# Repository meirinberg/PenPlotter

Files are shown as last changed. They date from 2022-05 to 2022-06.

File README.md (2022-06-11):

# Pen Plotter
<p align="center">
Mechanical Engineering 405 - Mechatronics <br> 
Term Project <br> 
Created by Mike Eirinberg, Ben Bradley, and Ryan Dean
</p>
<br>
<p align="center">
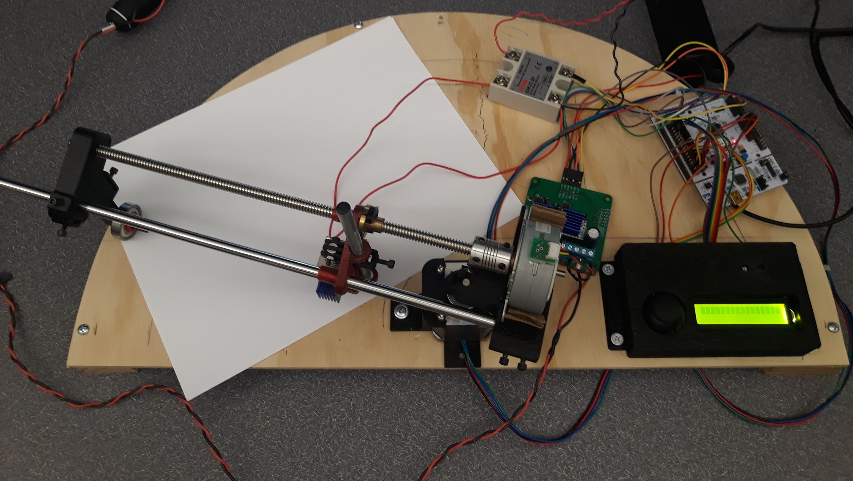
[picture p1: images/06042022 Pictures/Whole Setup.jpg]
  
</p>

## Demonstration
A demonstration of our pen plotter can be found using the following links. The first link demonstrates all features of our pen plotter and its attempt to draw a triangle. As discussed in the video, the motors provided by our mechatronics course were old and occasionally lock up. As a result, sometimes the drawing can't be finished. However, the second video shows a successful demonstration of the plotter drawing a triangle.

Pen Plotter Demonstration and Triangle-Drawing Attempt: <br>
https://youtu.be/bnkg2Q-DLaM

Succesful Triangle-Drawing Attempt:<br>
https://youtu.be/nqa20NQLPtA

## Project Background

In mechatronics, we were tasked with creating a 2.5 degree-of-freedom non-Cartesian pen plotter with the following rules. The pen plotter: 

1. Must be able to draw something
2. Must move in two different degrees of freedom (non-Cartesian)
3. Must use stepper motors for 2 axes
4. Must run off of 24V benchtop power supplies drawing no more than 6A
5. Must be safe (generally no lasers, fire, or hazarderous systems)

## Proposal
This project uses basic polar coordinates to accomplish drawing. The following image displays our initial sketch of our project’s hardware. Even though the structure of each component has been substantially refined, the core function can still be demonstrated in the sketch. It consists of a pivot point in the ‘Angular Subsystem’ sketch serving as the origin about which all major drawing components rotate. The ‘Radial Subsystem’ is an arm that extends overhead across the drawing area and provides structure for moving the pen. At the end, there is a T-shaped support structure with a wheel on the bottom. The wheel minimizes the friction required to start rotating the radial subsystem about the angular subsystem. We decided to use a support structure, because without it there would be a moment experienced by the angular motor rotor when the pen holder would be greatly extended in the radial direction. This could ultimately make it more difficult to move the motors and add drooping to the system. The next subsystem is the pen holder. This holds and activates the pen as it, using a lead screw, moves along the radial subsystem. The pen is pressed down by a solenoid upon activation.

<p align="center">
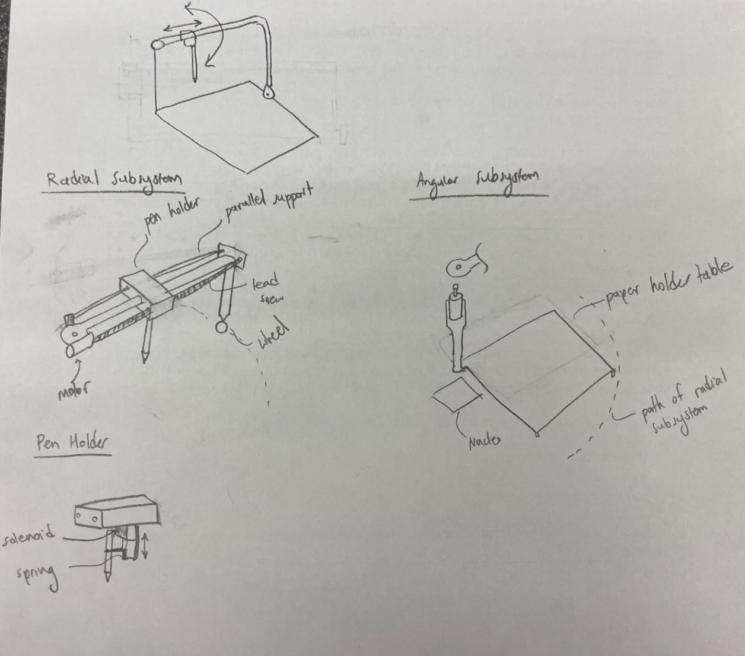
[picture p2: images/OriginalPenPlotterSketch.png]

</p>
<p align="center">
Figure 1. Initial sketch of pen plotter system
</p>

## First Iteration Challenges
We decided to use a 3D printer to create the parts that interact with the motors. Our first prints revealed critical flaws in our design. The first iteration prints can be seen below.
<p align="center">
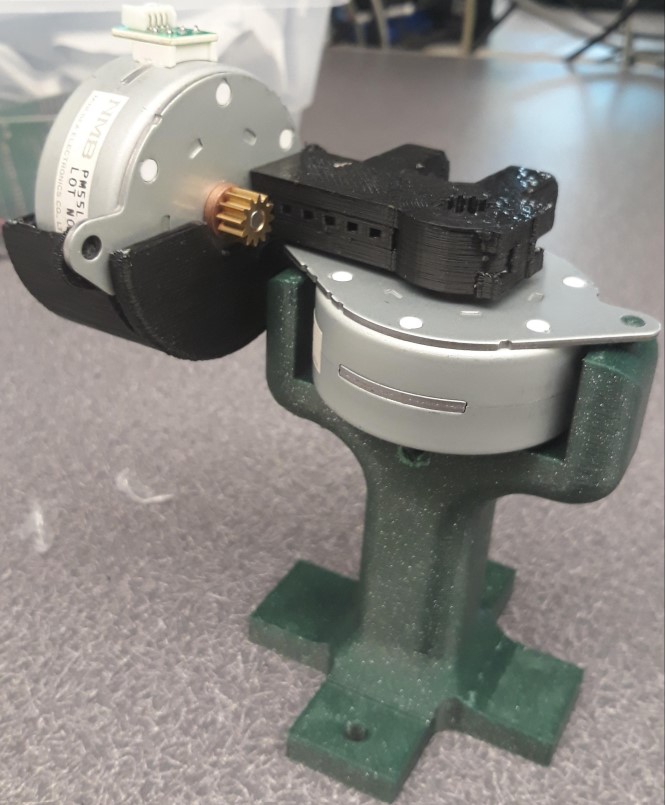
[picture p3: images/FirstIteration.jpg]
  
</p>
<p align="center">
Figure 2. First iteration 3D prints with radial and angular motor
</p>
We discovered that the pen plotter's resolution would face significant issues. Upon considering the dimensions of our drawing space, we realized that the angular motor would need to have very high accuracy. This is because resolution decreases as the pen moves farther out radially with each angular change. The provided motors only have 48 steps per revolution (7.5 degrees/step). This was far too low for our design, so we found a NEMA 17 stepper motor with 200 steps (1.8 degrees/step). This was a critical design challenge, because it caused us to change most radial motor design. The radial motor had to be properly secured. However, we did not change the radial motor to a NEMA 17 because our lead screw had a pitch of 2mm. Because of this, even with 48 steps, this small pitch allowed for higher resolution radial advancement. The pitch forced the radial motor to spin a lot to move linearly along the lead screw.

## Construction and Final Design
### Mechanical Design
A CAD model of our final design can be seen below. All part files and assemblies can be found in the 'parts' folder. See the images below for more details. Our construction consisted of 3D printing virtually all parts or reusing parts from past projects. A lead screw set, solenoid, and joysick were the only purchased parts.
<p align="center">
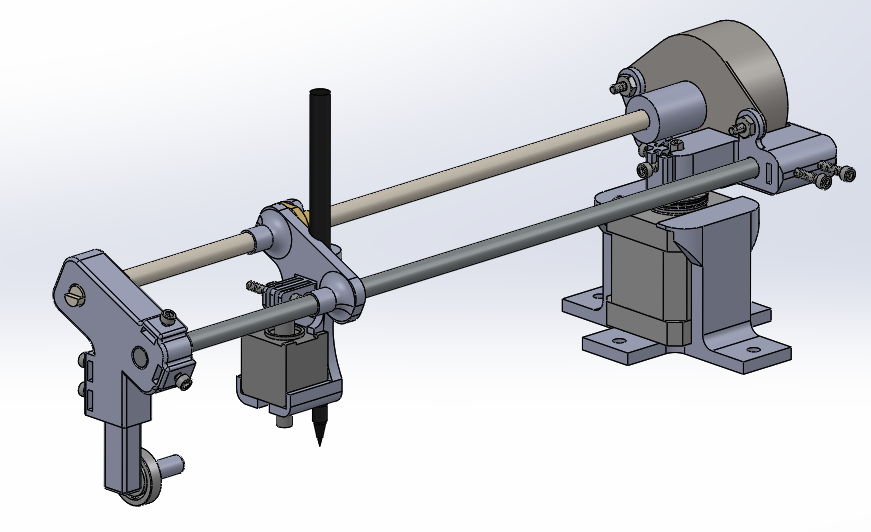
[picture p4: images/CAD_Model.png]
  
</p>
<p align="center">
Figure 3. CAD model of final design
</p>

Our final design closely follows the core concept of our initial sketch and accounts for the different geometry of using a NEMA 17 motor in our angular subsystem. This angular system is mounted in the center of a semicircle drawing canvas, and angularly rotates the radial system at its base to sweep angularly across the drawing area. We do not make use of the entire semicircle, since part of it will be used as space for the electronics. 
<br>

Our final design still consists of a solenoid to actuate the pen as well as a set screw for finding optimal pen height. It is critical for the design of this system to minimize friction, which may prevent the pen from actuating. This is because a solenoid has a starting force when it first begins to move and a holding force when it is fully extended. The starting force is the smallest since the solenoid is just beginning to actuate and can't experience the full effect of the induced magnetic field. Providing adequate clearance and guide structures allow for the pen to be rigidly actuated under the starting force. Our angular (theta) motor’s mount has a wide base to provide as much support as possible. Thrust bearings are used between the theta and radial motor assembly to further minimize angular friction during drawing. 
<br>

Because of the shaft-support structure, we don’t have to worry about the large moment created on the theta motor when the pen is far out along the lead screw, but this also increases the moment of inertia, making it harder for the theta motor to start rotating. A big design consideration was to make the system as adjustable as possible. There are many set screws around the assembly to make it easier to adjust lengths, heights, and replace components. The rest of the system is labeled below. 

<p align="center">
  
   
</p>
<p align="center">
Figure 4. Labeled components of mechanical design
</p>

### Electrical Design
Looking at the electrical components of our project, we were provided a Nucleo L476RG and a custom-made power board with a TMC4210 and TMC2208 motor driver per stepper motor. The TMC4210 interprets position, velocity, and acceleration commands, then sends step and direction signals to the TMC2208. The TMC2208 then takes this information and sends the appropriate current to the stepper motors. For each TMC2208, the voltage reference (Vref) needs to be set to create an internal current limit for the electrical components and stepper motors. We adjusted this by twisting a screw on the TMC2208 until we measured 0.7V. Datasheets for these components can be found in the folder above.

A 24V power supply is hooked up to the power board to supply power to the motors. For the solenoid, we used a solid-state relay and a separate power source, because of the solenoid's different power requirements. As seen in the image below, a joystick and LCD were also used as a user interface. As will be discussed later, these work together to select drawing files and control the free-draw feature.
<p align="center" float="left">
  
</p>
<p align="center">
Figure 5. Labeled components of electrical design
</p>

## Wiring Diagram
We used pinhole soldier boards for our hardware with trimmed leads. This ensured that we would not have a faulty connection, due to poor breadboard conductivity, while minimizing our resistances through smaller wires. This resulted in a wiring that never faultered. This wiring is modeled below. We communicate with our hardware using [Thonny](https://thonny.org/) connected to a laptop through a usb to micro usb connection. This powered our microcontroller, the STM32, which was the brains of our project. The STM32 had an attached "Shoe of Brian" to allow us to use micropython for this project. We utilized micropython to poll our joystick and send data to our LCD. The STM32 also controlled the pen through a solenoid that was attached to a relay. The power board contained two TMC4210s and two TMC2208s.  

<p align="center">
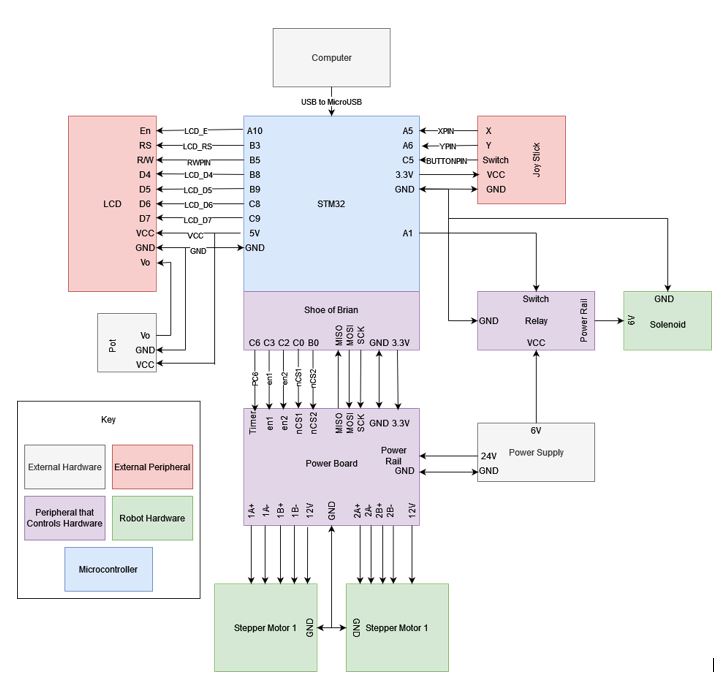
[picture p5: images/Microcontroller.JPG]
  
</p>
<p align="center">
Figure 6. Detailed wiring diagram
</p>

## Software Design and Implementation
Our code was structured as a finite state machine (FSM) using cooperative multitasking. We use five states, with the main four controlling the user interface, image processing, and sending motor commands in various modes. The FSM can be seen below with each state showing its task period and priority. The scheduler works by running based on frequency and priority, running the highest priority task at each call. Each state’s implementation will be discussed in further detail below.
<p align="center">
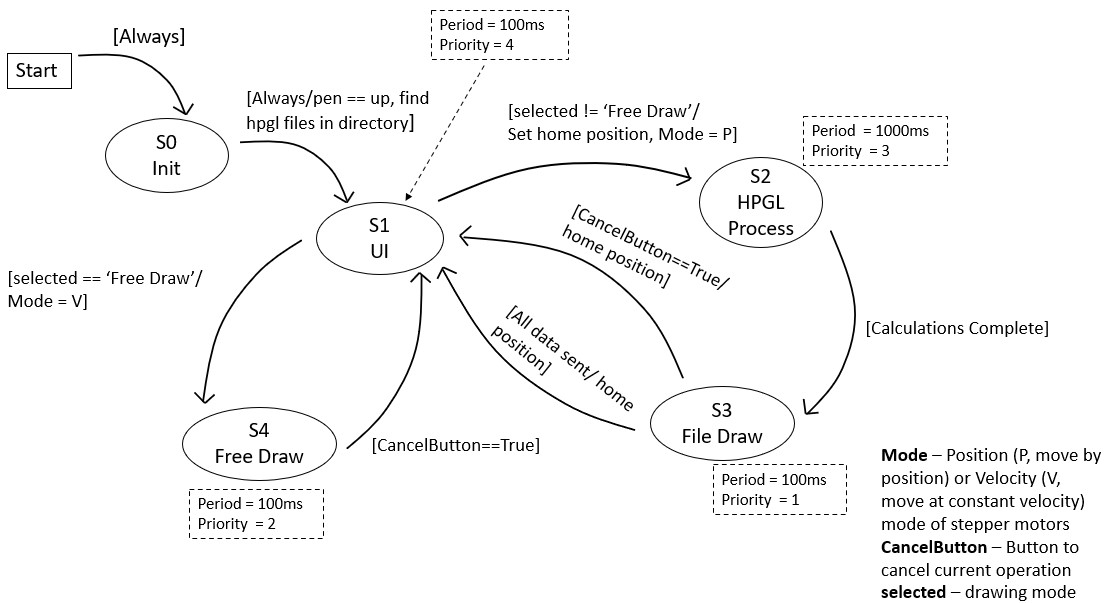
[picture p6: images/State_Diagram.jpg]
  
</p>
<p align="center">
Figure 7. State transition diagram
</p>

### S1 – User Interface
We designed our program to include an LCD-based user interface. This took some thoughtful programming. The user can scroll through the list of options by using the joystick axes and clicking the joystick to make a selection. Using the custom LCD class that we programmed, we sent one menu item to each line of the screen. We added a ">" character to prefix one menu option as a way for the user to highlight the item they wished to select. The program uses indexing to know which choice the user has highlighted and selected. To implement the scroll look, the program chooses which items to present in the list, one for each line. If the user has reached the top or bottom of the list, the scrolling ability stops.

The first menu item is always "Free Draw," which will put the program into that mode when selected. The next menu items are loaded from a basic file explorer function we programmed. The file explorer opens the current directory and finds the files with a .hpgl extension. It then lists those HP-GL files as the next menu items. Clicking an HP-GL file will cause the program to run file-draw mode using that filename.

The blue button on the STM32 microcontroller acts as our in-print cancellation button. By clicking this button during an active print, the pen plotter will return to its starting position and display the main menu user interface. When pressed during the free-draw mode, it will only cancel the mode, but not return to any position.

### S2 – Image Processing
This state receives the file name selected in the user interface to read the appropriate HP-GL data from a file stored on the board. The image-processing state can take a long time depending on the complexity of the image. Therefore, it was given the largest period in our task manager. This state calculates all required motor position data in one go and stores it as a global variable to be accessed from the file-draw state. 

All image-processing code was derived using the [Newton Raphson](#newton-raphson) method based on [Kinematic](#Kinematics) analysis. This analysis is discussed later. A key part of image processing was using linear interpolation. Due to the requirements of the system, the motors will spin at different rates. This means that over long distances, the motors can reach their target location at different times. This warps the image, so interpolation between the data points can be used to offset the effect. We first looked at the distance between points and saw if they passed certain thresholds. Various thresholds require different degrees of interpolation, with larger distances requiring more data points. This is accomplished using the linspace() function inherent to Python. Once interpolated and with the values added back to the original set, the data could then be sent to the file-draw state.

### S3 – File Draw
Once image processing is complete, this state will index through all the motor angle data and send the commands to the power board's drivers to run the stepper motors. Once the command is sent, our code reads the current position of the motors and will only continue indexing once they have reached their desired positions. The stepper motors are initialized in ramp mode for this state, since we need to send position data.

### S4 – Free Draw
The free-draw mode allows for manual drawing using a joystick. The user can control the pen-plotter directly, drawing anything they desire. X-direction joystick motion controls the theta motor while the Y-direction joystick motion controls the radial motor. Clicking the joystick will actuate the solenoid to force the pen up or down onto the paper. The stepper motors are initialized in velocity mode for this state and a virtual threshold for the joystick was hardcoded. This means that when the joystick passes a certain point, the motors will move at constant velocity. The threshold also helps with noise, as a resting joystick without a threshold could sporadically send signals.

## Kinematics

We used the following image to determine the calculations for our system. The image is viewed from the top looking down onto the drawing board. The ${\theta_1}$ represents the angular change of the arm while ${\theta_2}$ represents the angular change of the radial motor required to move the pen in the radial direction. This analysis should align with any polar-based system. 

<p align="center">
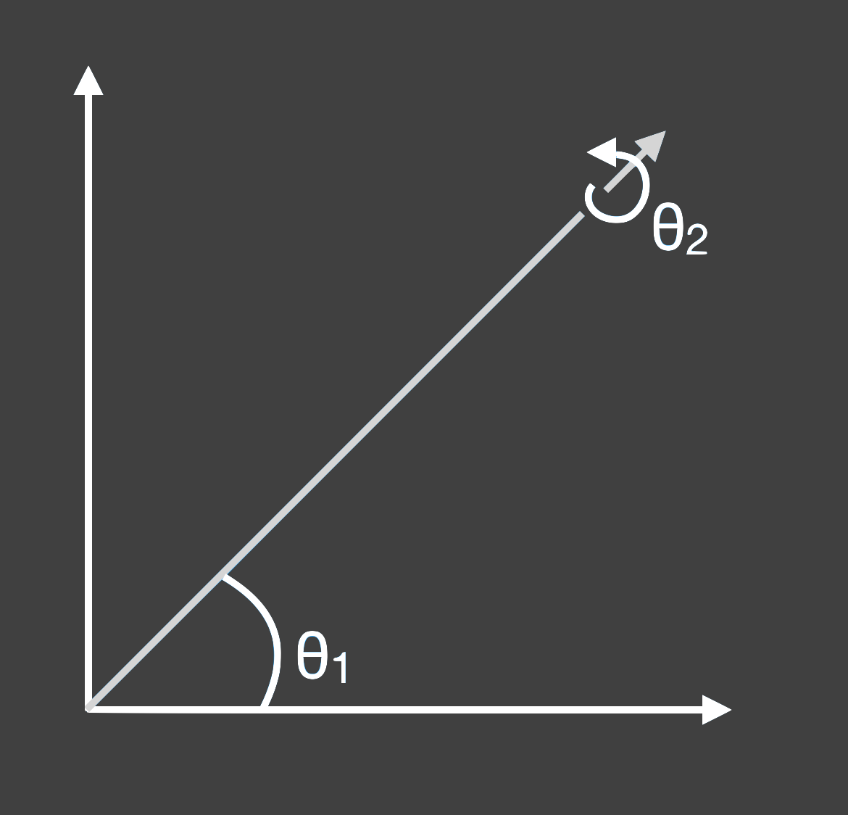
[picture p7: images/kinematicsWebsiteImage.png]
  
</p>
<p align="center">
Figure 8. Diagram of primary variables used in kinematic analysis
</p>

The design of our robot follows the standard polar coordinate system. The two parameters are a radius, $r$, and an angle, $\theta$. Our robot was centered at the bottom of the semicircle drawing canvas.

Two stepper motors are used to drive both these variables. Thus, the proper stepping angles must be calculated to operate the system correctly. 

Our first parameter, $\theta$, is used by the first stepper motor to move the system angularly (denoted as $\theta_1$).

The radius parameter, $r$, moves along a lead screw with a 2mm pitch. By using the second stepper motor to rotate the lead screw, we can move to our desired radius. As such, we must calculate the stepper motor rotation needed to move a desired distance along the lead screw (denoted as $\theta_2$). We know that there are 25.4mm per inch, so that implies there are 12.7 threads per inch. Furthermore, $\theta_2 \cdot \frac{2mm}{2\pi} \cdot \frac{1 in}{25.4mm} = \frac{\theta_2}{\pi 25.4 in}$. This constant, $\pi \cdot 25.4$, (denoted as $\alpha$), is used below.

Recall the trigonometric relationship between Cartesian and polar coordinates: $x = rcos(\theta_1)$ and $y = rsin(\theta_1)$

Initial Matrix:

$\begin{bmatrix}x \newline y \end{bmatrix}$= $\begin{bmatrix}  \frac{\theta_2}{\alpha} & cos(\theta_1) \newline  \frac{\theta_2}{\alpha} & sin(\theta_1)\end{bmatrix}$ 

$x = f(\theta)$

Jacobian Matrix:

$\frac{\partial f}{\partial \theta}$ = $\begin{bmatrix}  \frac{\partial f_1}{\partial \theta_1} & \frac{\partial f_1}{\partial \theta_2}\newline  \frac{\partial f_2}{\partial \theta_1} & \frac{\partial f_2}{\partial \theta_2}\end{bmatrix}$  

$\frac{\partial f_1}{\partial \theta_1} = -\frac{\theta_2}{\alpha}sin(\theta_1)$ &emsp; &emsp; $\frac{\partial f_1}{\partial \theta_2} = \frac{1}{\alpha}cos(\theta_1)$  

$\frac{\partial f_2}{\partial \theta_1} = \frac{\theta_2}{\alpha}cos(\theta_1)$ &emsp; &emsp; $\frac{\partial f_2}{\partial \theta_2} = \frac{1}{\alpha}sin(\theta_1)$

Find the velocity kinematics by differentiating x = f(θ) with respect to time:

$x = \frac{d}{dt}(f(\theta))$

$ \frac{df_1}{dt} = \frac{d}{dt}[\frac{\theta_2}{\alpha}cos(\theta_1)] = \frac{1}{\alpha}cos(\theta_1) - \frac{\theta_2}{\alpha}sin(\theta_1)$ &emsp; &emsp; &emsp; &emsp; $ \frac{df_2}{dt} = \frac{d}{dt}[\frac{\theta_2}{\alpha}sin(\theta_1)] = \frac{1}{\alpha}sin(\theta_1) + \frac{\theta_2}{\alpha}cos(\theta_1)$

$x$ = $\begin{bmatrix}  -\frac{\theta_2}{\alpha}sin(\theta_1) & \frac{1}{\alpha}cos(\theta_1)\newline  \frac{\theta_2}{\alpha}cos(\theta_1) & \frac{1}{\alpha}sin(\theta_1)\end{bmatrix}$ 
$\begin{bmatrix}  \frac{1}{\alpha}(cos(\theta_1) - \theta_2sin(\theta_1) \newline  \frac{1}{\alpha}(sin(\theta_1) + \theta_2cos(\theta_1)\end{bmatrix}$ 

$x$ = $\begin{bmatrix}  -\frac{\theta_2}{\alpha}sin(\theta_1)[\frac{1}{\alpha}(cos(\theta_1) - \theta_2sin(\theta_1)] +  \frac{1}{\alpha}cos(\theta_1[\frac{1}{\alpha}(sin(\theta_1)+\theta_2cos(\theta_1)]\newline  \frac{\theta_2}{\alpha}cos(\theta_1)[\frac{1}{\alpha}(cos(\theta_1) -\theta_2sin(\theta_1)] +  \frac{1}{\alpha}sin(\theta_1)[\frac{1}{\alpha}(sin(\theta_1)+\theta_2cos(\theta_1)]\end{bmatrix}$ 

Inverse Kinematics:

$y = x - f(\theta) = g(\theta)$

$\frac{\partial g(\theta))}{\partial \theta} = \frac{\partial}{\partial \theta}[0-f(\theta)]$

$\frac{\partial g(\theta))}{\partial \theta} = -\frac{\partial}{\partial \theta}f(\theta)$

## Newton Raphson

The Newton Raphson method was used to find the proper motor angular position data to produce desired rectilinear coordinates. This method is typically used to find the roots of a function. Rather than use the function directly derived from our kinematic analysis, we needed to slightly modify our position matrices to allow for solving for specific points. This is done by taking our kinematic analysis output and subtracting it from the desired position. This function can then have its roots solved for where each root corresponds to the desired and actual motor positions converging. The output results in angular data we can send to the motors. More information on this method can be found [here](https://en.wikipedia.org/wiki/Newton%27s_method). 

Once the image was processed, we verified our analysis by plotting motor angular data and final plotted positions. As can be seen below, there are no discontinuities in the outputs and our final plot matches the desired triangular image exactly. A GIF was also constructed to show the plotter’s motion as it plots, with the blue line representing the arm of the system and the red lines representing the drawn pen lines. The final image shows the triangle that our pen plotter was able to accomplish.

<p align="center">
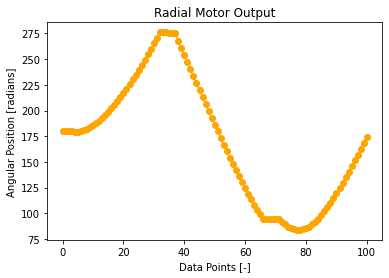
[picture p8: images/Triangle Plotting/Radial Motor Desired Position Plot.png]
  
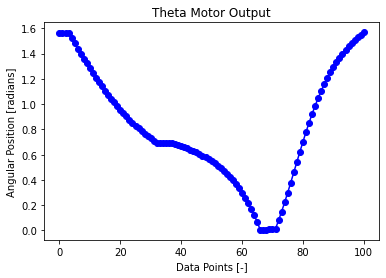
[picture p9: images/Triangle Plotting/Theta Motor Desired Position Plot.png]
  
</p>
<p align="center">
Figure 9. Plots of radial (left) and angular (right) motor output position
</p>
  
<p align="center" float="left">
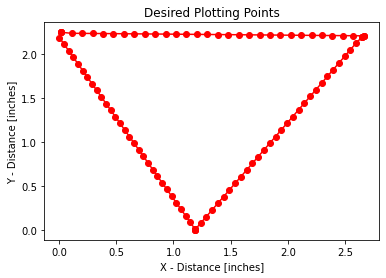
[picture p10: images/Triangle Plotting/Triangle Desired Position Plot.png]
  
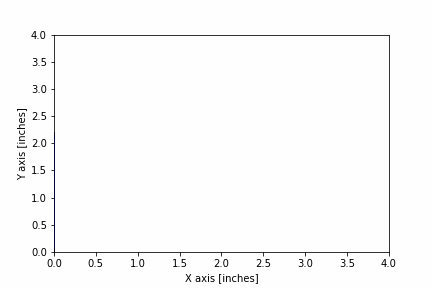
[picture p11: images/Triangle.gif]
  
</p>
<p align="center">
Figure 10. Desired pen plotter plots
</p>

## Results and Final Thoughts
Our project was successful in creating a functional pen plotter. The triangle, as discussed in the Newton Raphson section above, can be seen below. Clearly, the lines are not as smooth as we had hoped but would improve with more interpolated data points. However, the provided Nucleo does not have a large amount of storage available, so it can be difficult to find the right balance of image quality v. complexity.
<p align="center">
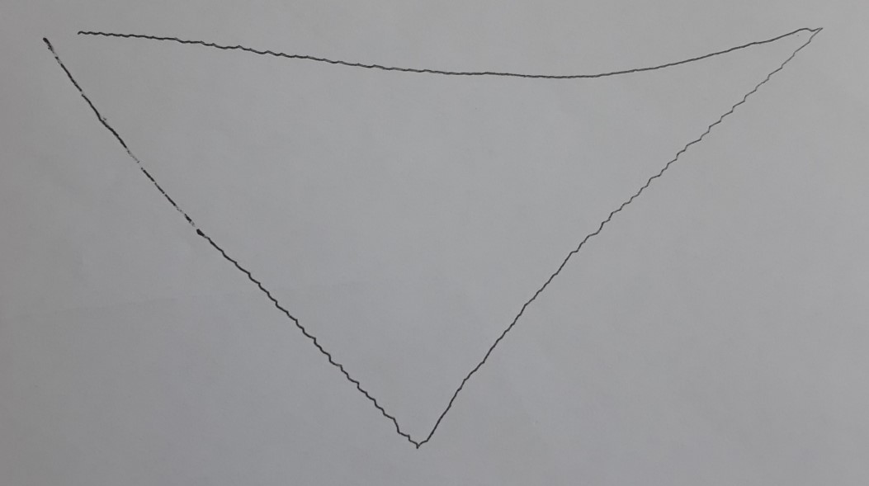
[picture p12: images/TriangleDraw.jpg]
  
</p>
<p align="center">
Figure 11. Pen plotter output from triangle input image
</p>
Unfortunately for the free drawing state, there is some delay between an input from the joystick and motion of the motor. This can be mostly attributed to the added weight of all mechanical components. It can be difficult to angularly accelerate a mass with a high moment of inertia, leading to a delayed start and stop reaction time. A future design could involve optimizing the weight of the radial arm and eliminating the shaft support. Finally, the biggest issue we encountered was the reliability of the provided radial motor. We found that after some time, the motors would lock up and refuse to rotate, only to start rotating moments later. This made it difficult in the beginning to know if there was a software or hardware issue, so we recommend that anyone starting a project like this ensure their motors can handle the required load.

## Component Walkthrough

### Microcontroller

We used the STM32L476RG as our microcontroller. The microcontroller has 128KB ram and 1Mb flash. We are able to fully control our system with our microcontroller. We used micropython as our language of choice for this project with the Shoe of Brian attachment, in order to interface native C in the STM32 to micropython. The Shoe of Brian allows us to "flash" our micropython code to the STM32 board through a simple drag-and-drop on our personal computer.

### Stepper Motors

<p align="center">
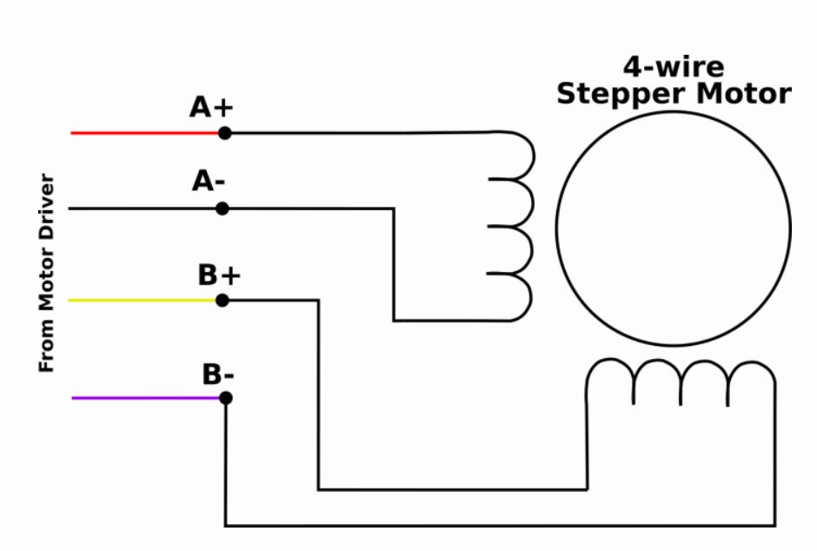
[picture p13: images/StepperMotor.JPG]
  
</p>

We used two 4-wire stepper motors with internals (shown below). By inducing a current, we were able to rotate our arm motor 48 individual steps for our radial stepper motor and 200 steps for our theta stepper motor. This allowed us to make fairly precise drawings, but did come with some troubles. We destroyed three 48-step motors, while our 200-step NEMA 17 motor survived. The 48-step motor tended to produce results that varied despite the code being the same at times. This repeatedly turned out to be a motor issue and not a code issue. We would recommend purchasing reliable stepper motors to save time and expense in future projects.

### Solenoid and Relay

<p align="center">
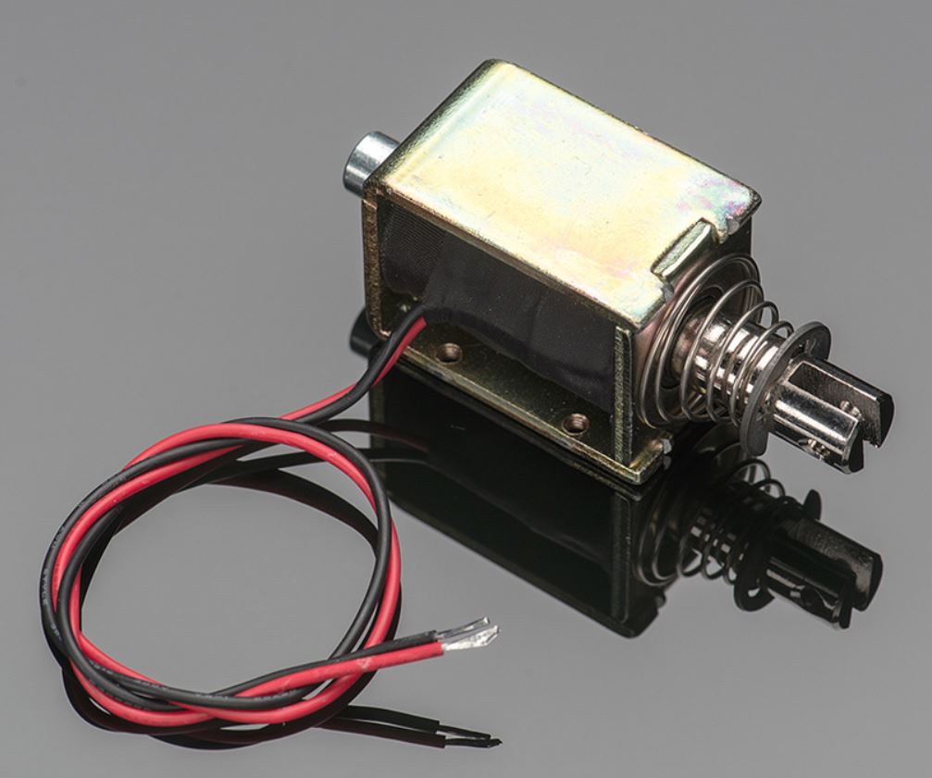
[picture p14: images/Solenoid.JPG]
  
</p>

We utilized a non-polar solenoid to control our pen-up and pen-down motions. We mounted the [solenoid to a rail](https://github.com/meirinberg/PenPlotter/blob/main/README.md#mechanical-design), so we were able to do pen-up and pen-down motions in any position in our radial and theta axes. We connected our solenoid to a relay, which worked flawlessly.
<br>
<br>

### Power Supply 

<p align="center">
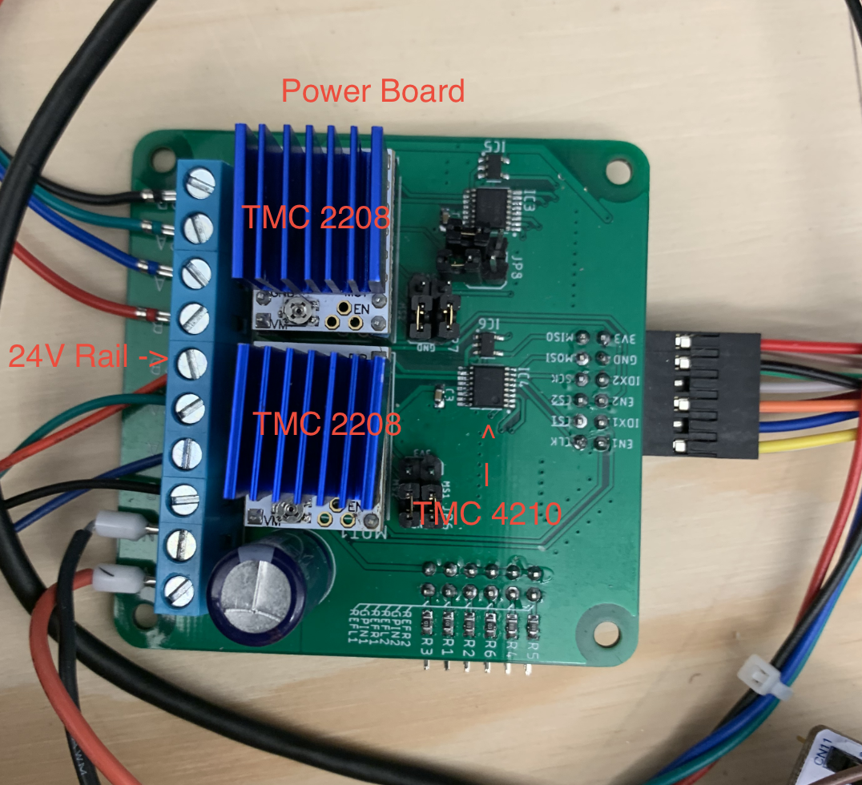
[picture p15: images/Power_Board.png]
  
</p>

We used a power board to control our stepper motors from one SPI configuration. We were able to do this by manually enabling which stepper was active, toggling the corresponding chip select. Additionally, our power board has an input of a 24V rail and supplies 12V to each motor. This aided in our wiring. The power board has two TMC4210 chips and two TMC2208 chips. TMC4210s were used for enabling and calculating TMC2208 commands. The TMC2208 chips are used to send the calculated commands directly to each motor. For more information on setting the TMC2208s current limit, [look here](https://wiki.fysetc.com/TMC2208/).

<br>
<br>

### LCD

<p align="center">
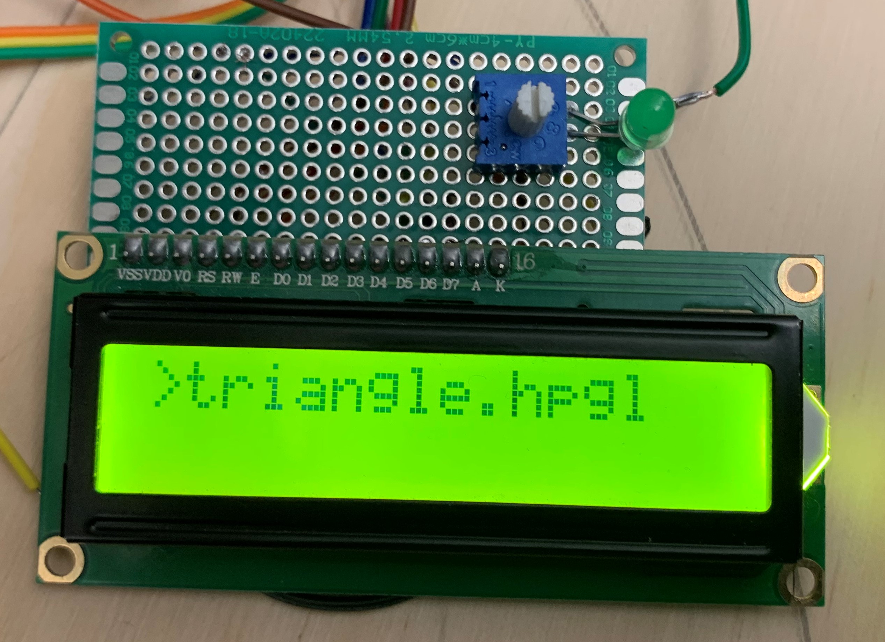
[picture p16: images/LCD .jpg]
  
</p>

The LCD board is configured in 4-bit mode. The LCD class was written manually, by using delays and bit-banging pins. Initially, we thought the use of delays would slow down our pen plotter's other functions. However, we were able to reduce the delay to 0.0005 seconds, which made the delay negligable. Unfortunately, 4-bit mode requires more wiring connections than an LCD with an I2C bus module. To reduce the large wiring footprint without an I2C configuration, we soldered our pin connections to a solder-board. This reduction in size allowed the LCD to fit within the 3D-printed housing we designed for it. We attached a potentiometer to the LCD's Vo pin to enable the user to manually adjust the contrast of the LCD.

### Joystick

<p align="center">
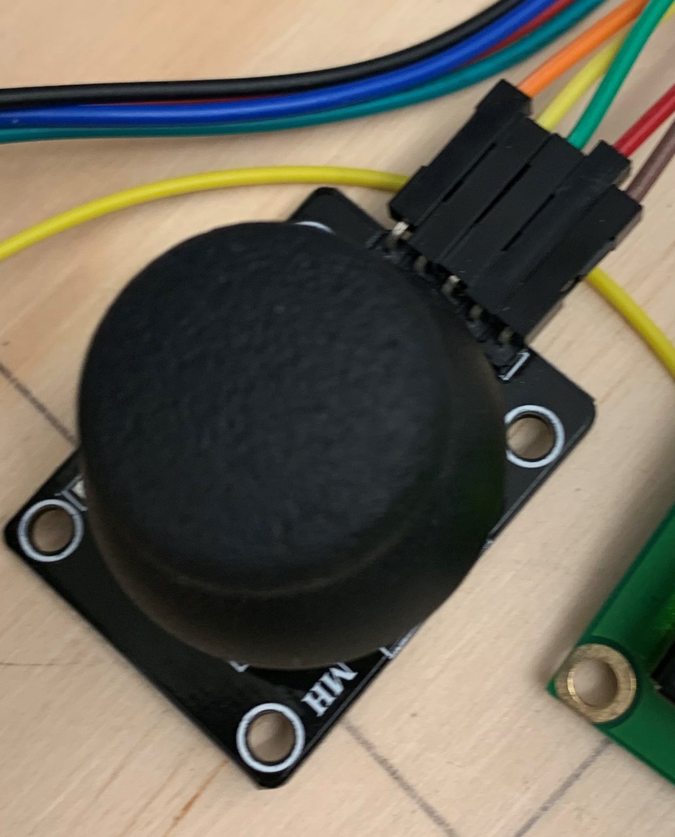
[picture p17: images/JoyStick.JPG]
  
</p>

The joystick employs two ADCs to read the X and Y axes from the joystick potentiometer. We used 3.3V to operate the joystick, even though it is rated for 5V. We found that operation at 3.3V was optimal because that voltage matched the internal reference voltage of the microcontroller's ADC. This allows for smooth movement tracking with the joystick. However, we did remove noisy inaccuracies at the joystick's center position by introducing a threshold. We configured three GPIO pins as inputs, two for the ADCs, and one for the joystick's button. We flipped some of the axes through programming, because our 3D-printed housing better accommodated the joystick upside down.

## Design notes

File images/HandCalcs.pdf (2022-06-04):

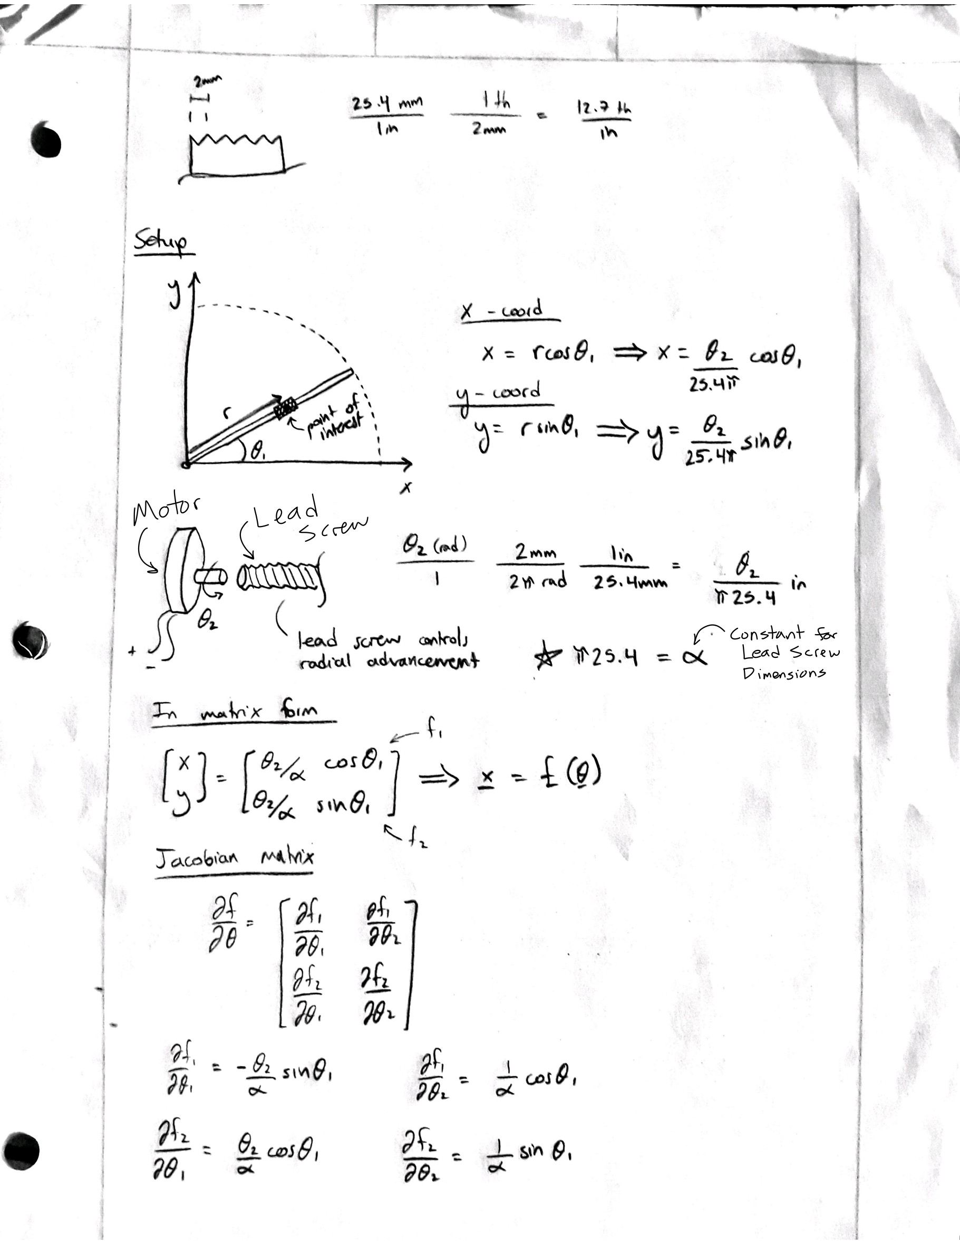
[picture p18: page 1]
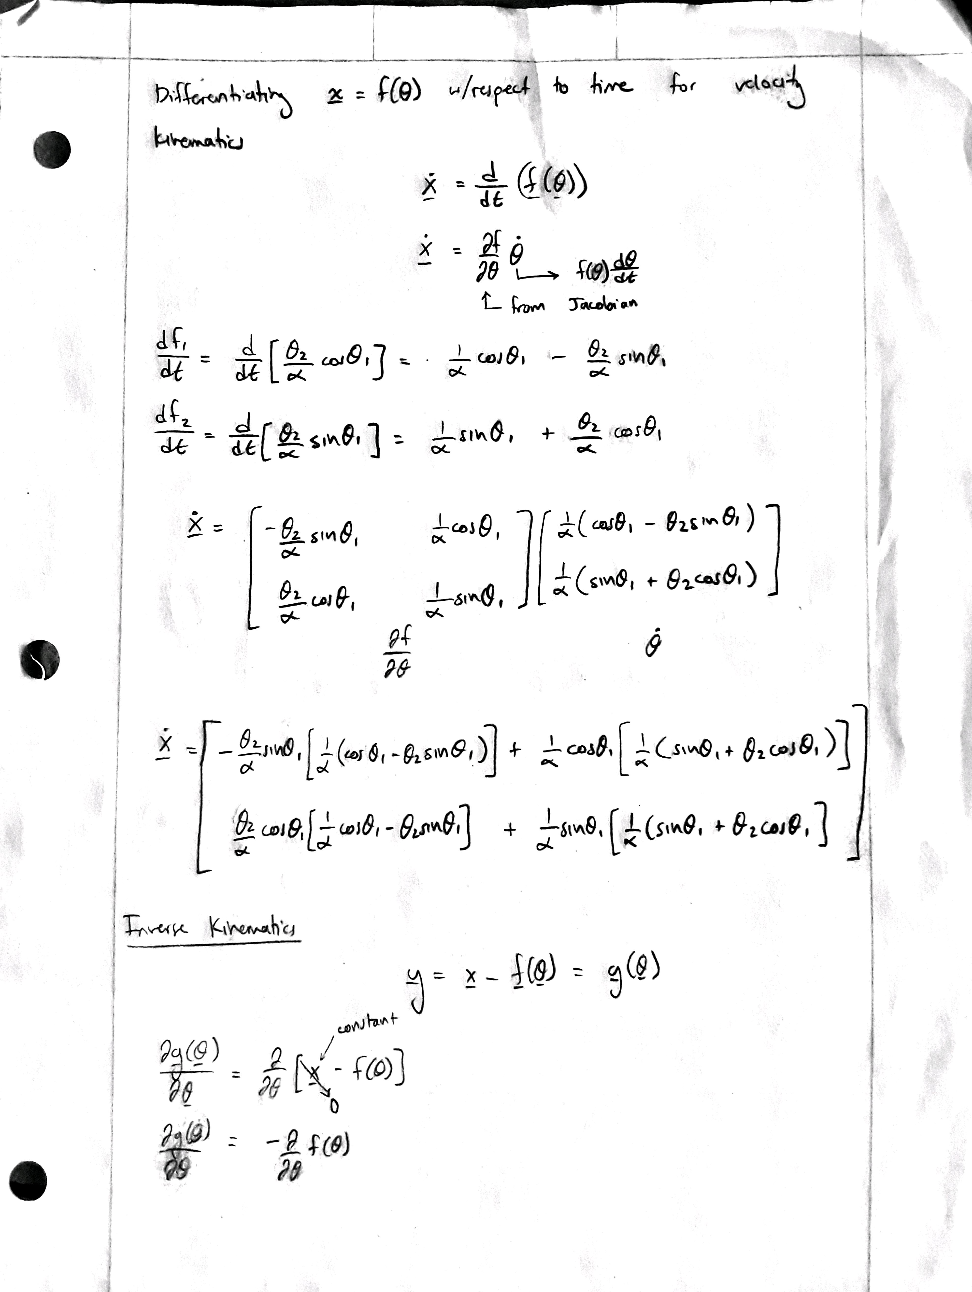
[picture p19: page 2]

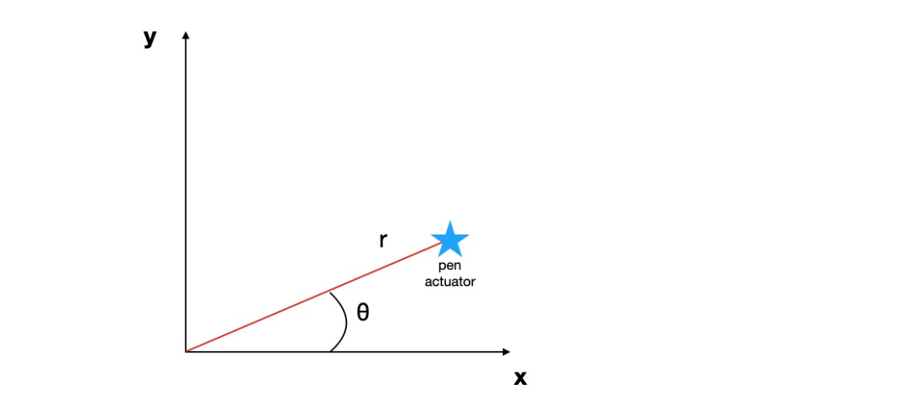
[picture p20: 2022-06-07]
images/OverallDesignDrawing.png

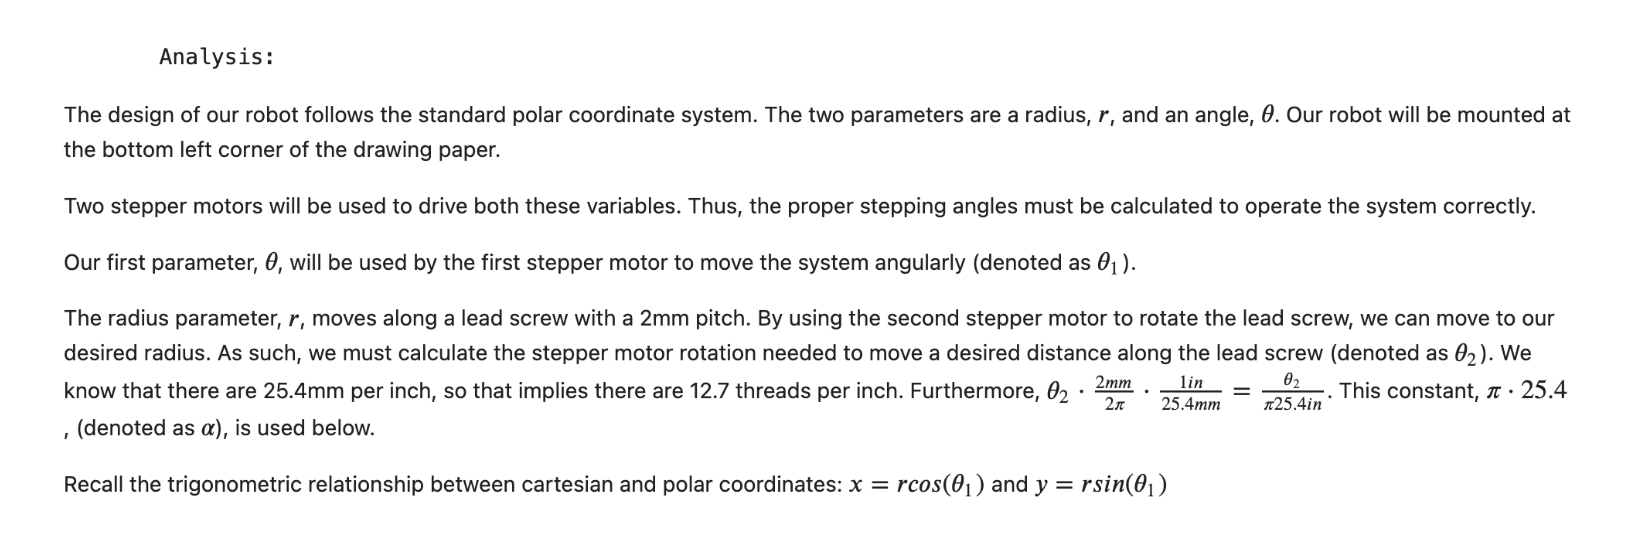
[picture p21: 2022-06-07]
images/kinematicsMath1.png

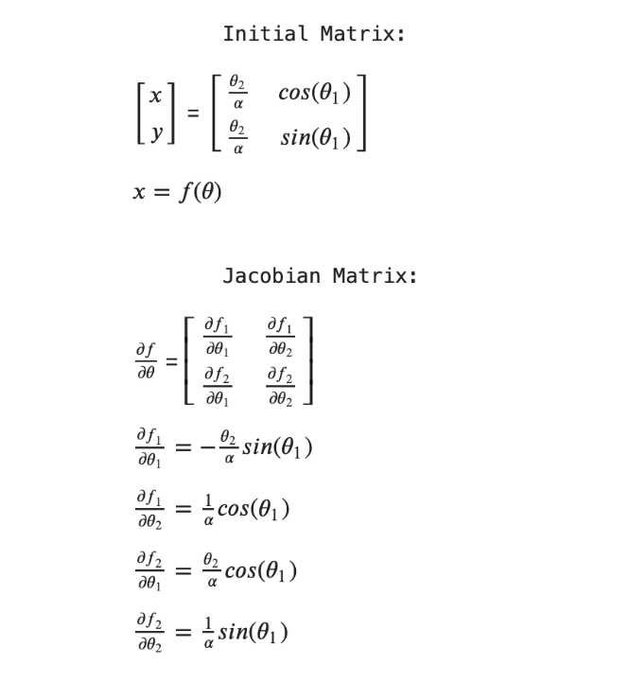
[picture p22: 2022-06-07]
images/kinematicsMath2.png

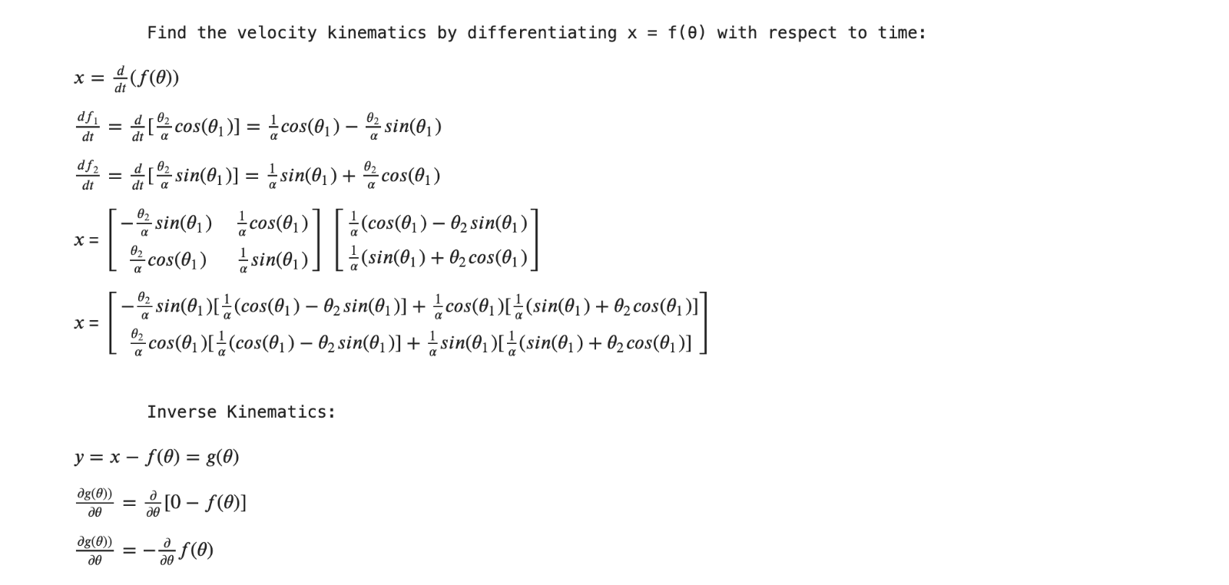
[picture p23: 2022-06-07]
images/kinematicsMath3.png

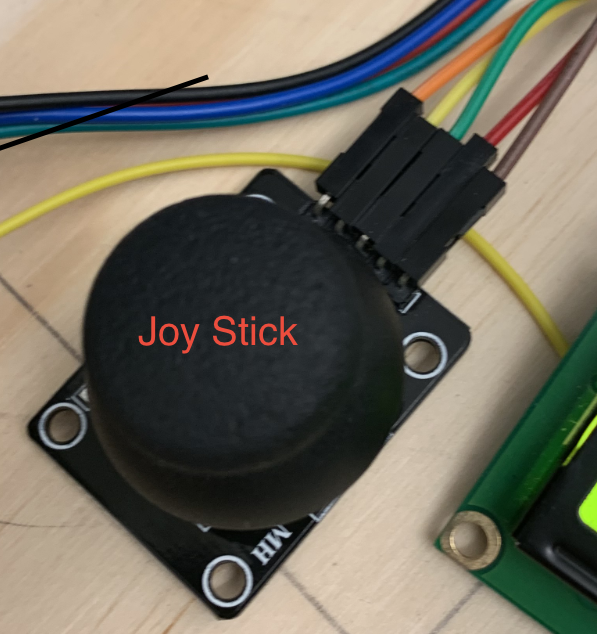
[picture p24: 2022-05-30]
images/Joy_Stick.png

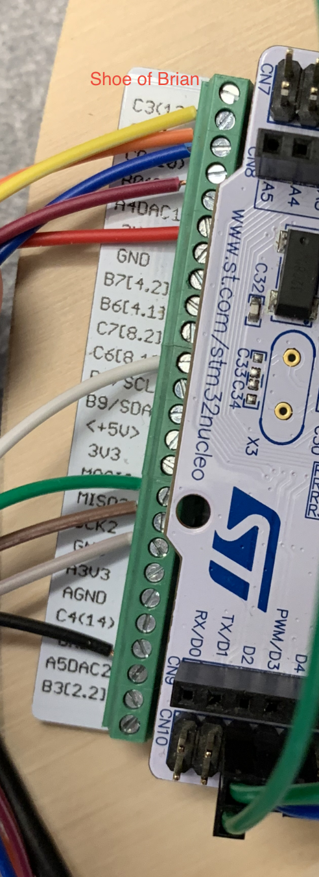
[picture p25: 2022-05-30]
images/Shoe_Of_Brian.png

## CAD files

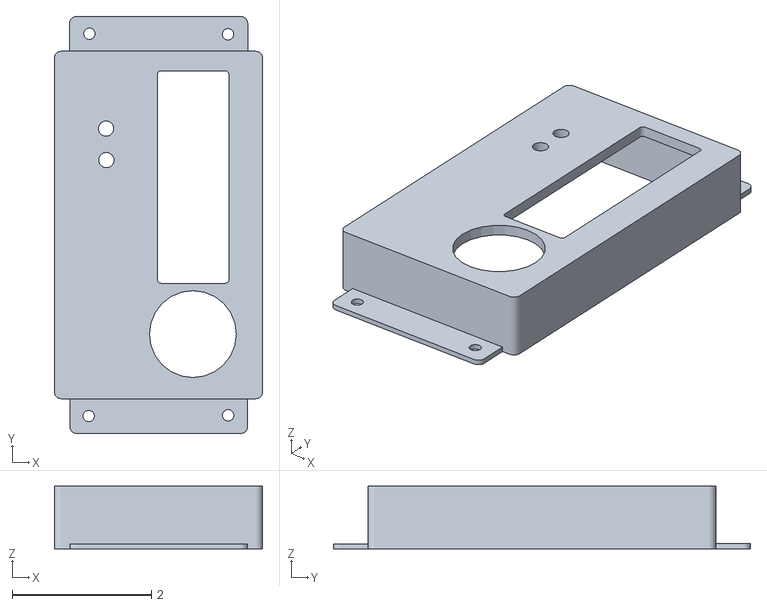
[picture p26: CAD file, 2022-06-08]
parts/LCDJoystickDisplay.stl
3.00 x 6.00 x 0.9

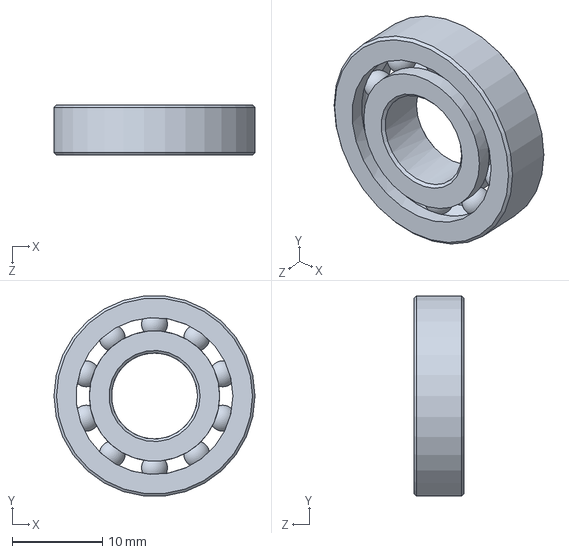
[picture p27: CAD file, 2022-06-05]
parts/Ball Bearing.SLDPRT
22.2 x 22.1 x 5.56 mm

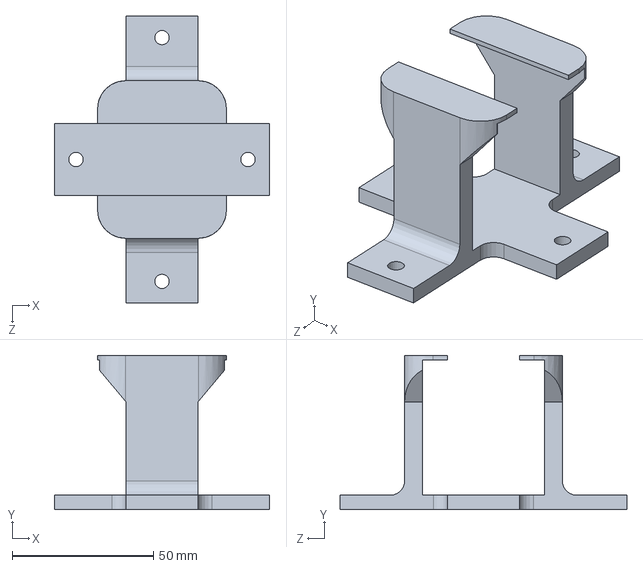
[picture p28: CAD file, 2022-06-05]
parts/ServoSupport.SLDPRT
76.2 x 54.6 x 101.6 mm

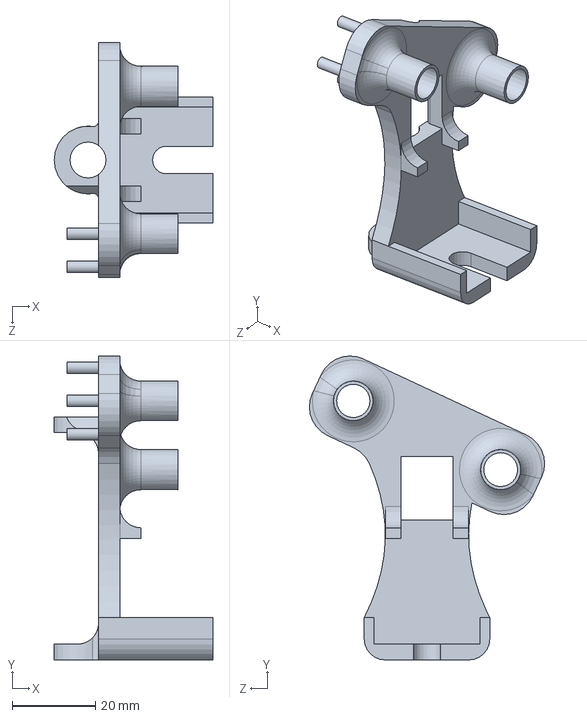
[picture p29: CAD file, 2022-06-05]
parts/Carriage_Solenoid.SLDPRT
38.1 x 73.0 x 56.5 mm

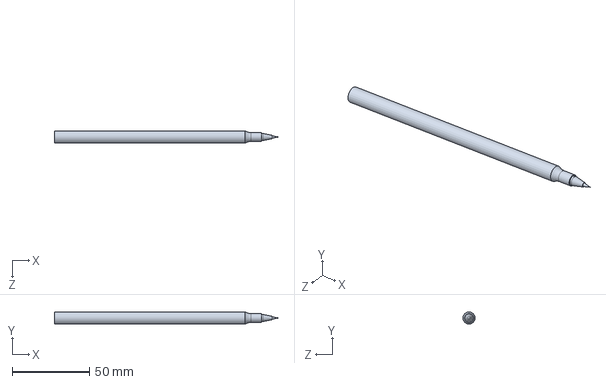
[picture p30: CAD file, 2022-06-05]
parts/Pen.SLDPRT
144.7 x 7.90 x 7.90 mm

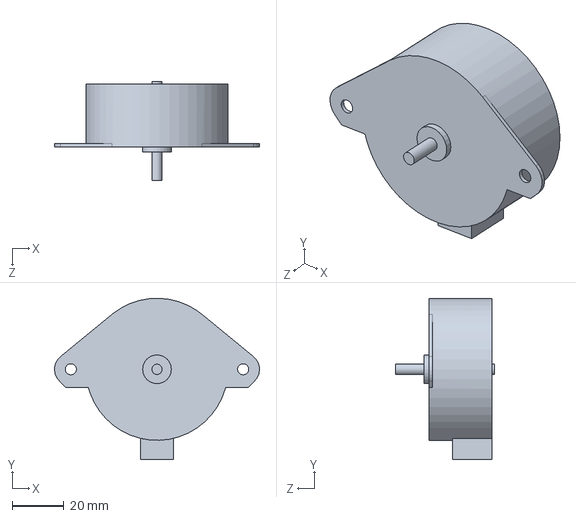
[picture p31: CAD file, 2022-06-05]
parts/ServoMotor.SLDPRT
79.4 x 62.5 x 38.2 mm

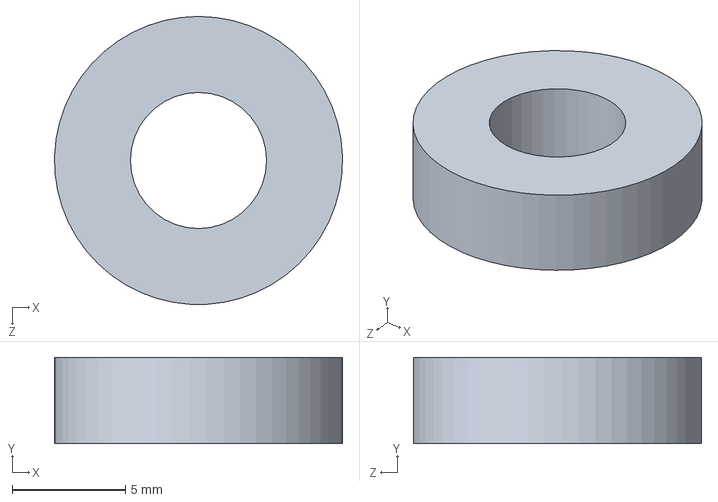
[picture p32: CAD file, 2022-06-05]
parts/Bearing_Spacer.SLDPRT
12.7 x 3.81 x 12.7 mm

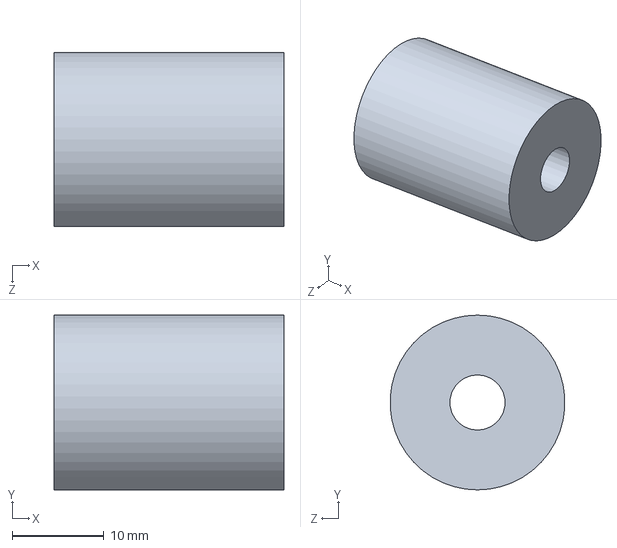
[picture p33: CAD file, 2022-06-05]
parts/Coupler.SLDPRT
25.0 x 19.0 x 19.0 mm

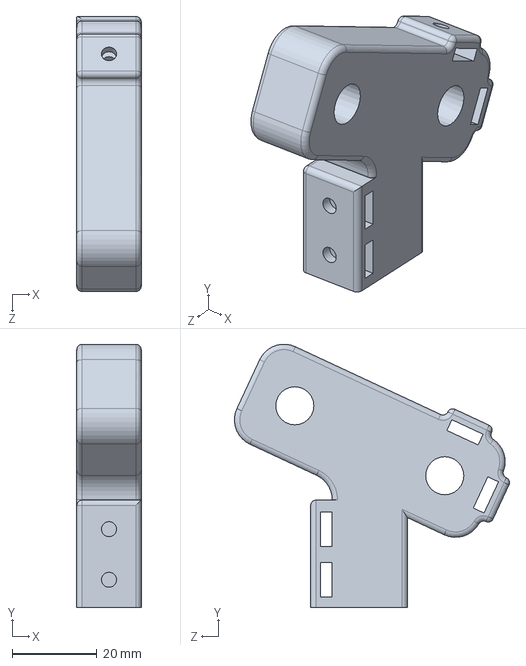
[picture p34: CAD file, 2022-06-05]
parts/BeamSupport_2.SLDPRT
15.2 x 62.2 x 64.9 mm

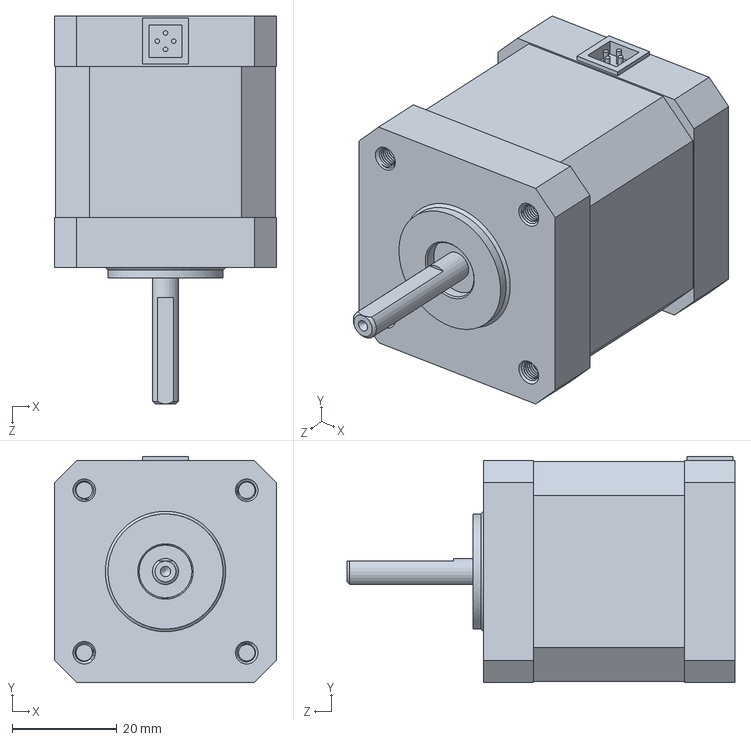
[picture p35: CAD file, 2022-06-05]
parts/NEMA17.SLDPRT
42.4 x 43.2 x 74.0 mm

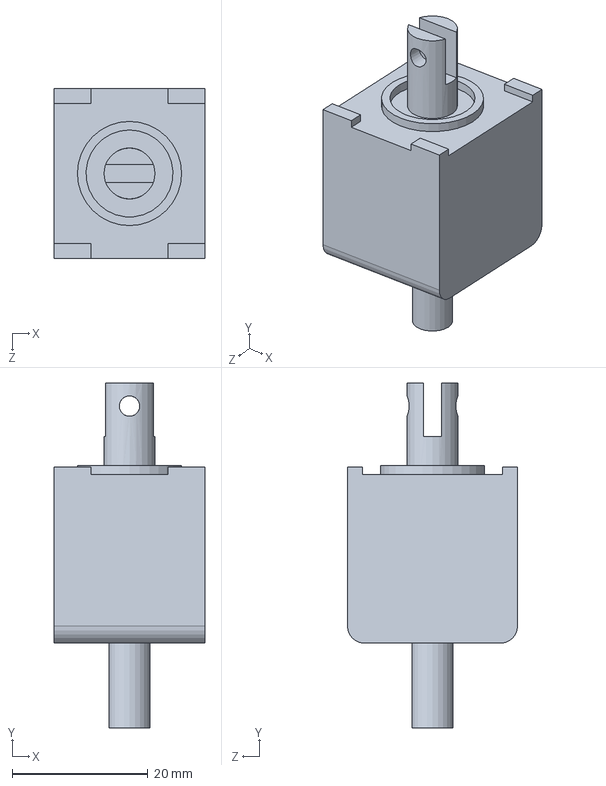
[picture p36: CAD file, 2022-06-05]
parts/Solenoid.SLDPRT
22.2 x 50.9 x 25.1 mm

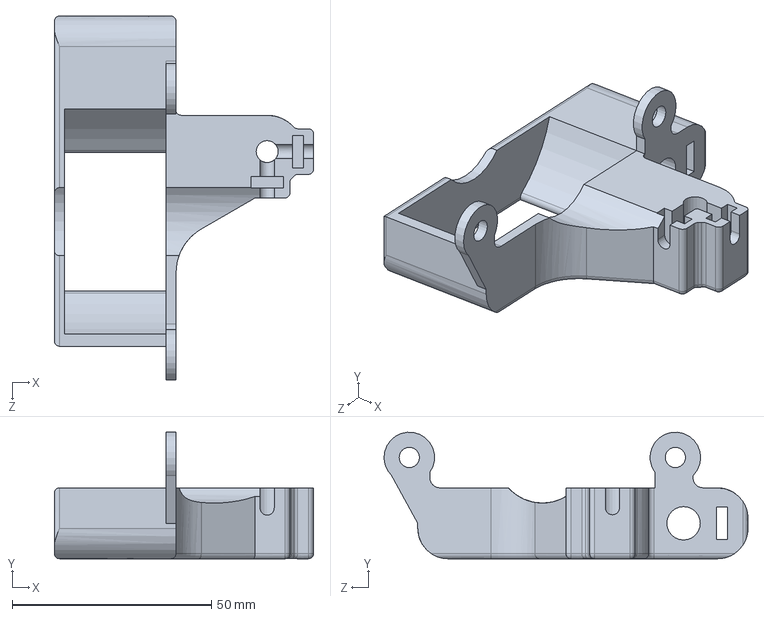
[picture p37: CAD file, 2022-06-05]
parts/Beam_2.SLDPRT
65.0 x 31.7 x 91.3 mm

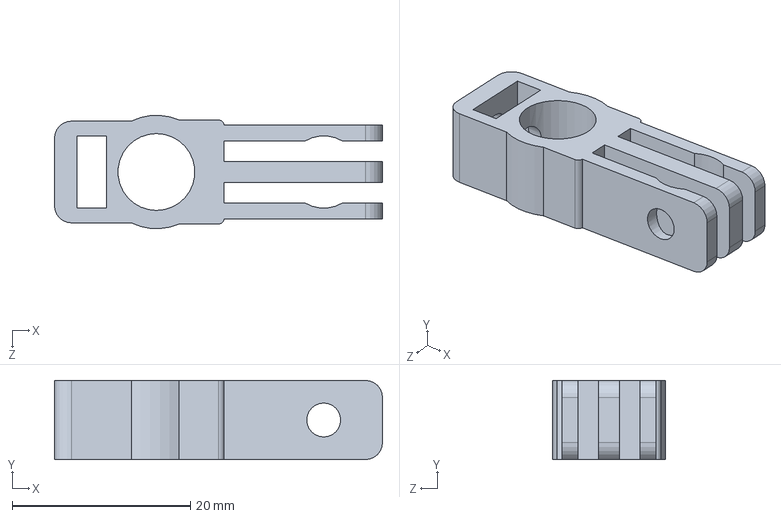
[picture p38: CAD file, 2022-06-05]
parts/Pen Holder.SLDPRT
36.9 x 8.89 x 12.7 mm

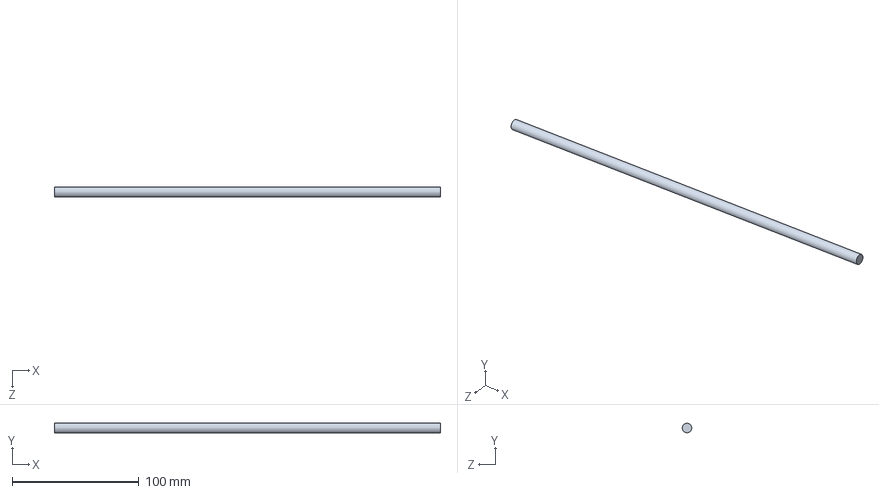
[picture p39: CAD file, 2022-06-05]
parts/ThreadedRod.SLDPRT
304.8 x 7.62 x 7.62 mm

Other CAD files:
parts/SlidingRod.SLDPRT
parts/BeamSupportAdjust.SLDPRT
parts/5909K31_Needle-Roller Thrust Bearing.SLDPRT
parts/94500A221_316 Stainless Steel Button Head Hex Drive Screws.SLDPRT
parts/90480A007_Low-Strength Steel Hex Nut.SLDPRT
parts/91251A148_Black-Oxide Alloy Steel Socket Head Screw.SLDPRT
parts/91251A153_Black-Oxide Alloy Steel Socket Head Screw.SLDPRT
parts/Bearing Washer.SLDPRT
parts/LCDJoystickDisplay.dwg
parts/Lead Screw Holder.SLDPRT
parts/LeadScrewCover.SLDPRT

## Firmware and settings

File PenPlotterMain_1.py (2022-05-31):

from ulab import numpy as np
import pyb
from pyb import Pin, Timer, ADC, ExtInt, SPI
import time
import math
from array import array
import os

dpi = 1016
maxWidth = 8*dpi
maxHeight = 11*dpi

alpha = 3.14159*25.4

# def interpolate(xdata, ydata):
#     # Interpolate values for x and y.
#     t = np.linspace(0, 1, len(xdata))
#     t2 = np.linspace(0, 1, 100)
#     # One-dimensional linear interpolation.
#     x2 = np.interp(t2, t, xdata)
#     y2 = np.interp(t2, t, ydata)
#     return x2,y2

def interp(xpoint,ypoint,num):    
    ix = np.linspace(xpoint[0],xpoint[1],num)
    iy = np.linspace(ypoint[0],ypoint[1],num)
    return ix, iy


def g(x, theta):
    # Computes difference between expected and calculated pen plotter angular position
    #print("Theta",theta)
    f1 = theta[1]*math.cos(theta[0])
    f2 = theta[1]*math.sin(theta[0])
    #print("X",x)
    Theta = np.array([f1,f2])
    return x-Theta
    
def dg_dtheta(theta):
    # Computes Jacobian matrix for inverse kinematics
    df1dt1 = -theta[1]*math.sin(theta[0])# /alpha
    df1dt2 = math.cos(theta[0])# /alpha
    df2dt1 = theta[1]*math.cos(theta[0])# /alpha
    df2dt2 = math.sin(theta[0])# /alpha
    jacob = np.array([[-1*df1dt1, -1*df1dt2],[-1*df2dt1,-1*df2dt2]])
    return jacob

def NewtonRaphson(fcn, jacobian, guess, thresh):
    # This is called repeatedly to iterate on the correct angular position to produce the desired
    # pen plotter position.
    steps = 1

    while (abs(fcn(guess)[0]) > thresh or abs(fcn(guess)[1]) > thresh):
        
        math = guess - np.dot(np.linalg.inv(jacobian(guess)),fcn(guess))

        guess = math
        steps += 1
    return guess

class LED: 

   def __init__(self):
      # Joystick Pin Connections
      self.LEDPIN = Pin(Pin.cpu.C4, mode=Pin.OUT)

   def on(self):
      self.LEDPIN.high()

   def off(self):
      self.LEDPIN.low()

   def getValue(self):
      return not self.LEDPIN.value()  # If this returns true, the LED is ON. Otherwise, the LED is OFF.

class Solenoid: 

   def __init__(self):
      # Joystick Pin Connections
      self.PENPIN = Pin(Pin.cpu.A1, mode=Pin.OUT)

   def down(self):
      self.PENPIN.high()

   def up(self):
      self.PENPIN.low()

   def getValue(self):
      return not self.PENPIN.value()  # If this returns true, the pen is down. Otherwise, the pen is up.


class Joystick: 

   def __init__(self):
      # Joystick Pin Connections
      self.XPIN = Pin(Pin.cpu.A5, mode=Pin.IN)
      self.YPIN = Pin(Pin.cpu.A6, mode=Pin.IN)
      self.BUTTONPIN = Pin(Pin.cpu.C5, mode=Pin.IN, pull=pyb.Pin.PULL_UP)
      self.x = pyb.ADC(self.XPIN)    # create an analog object from a pin
      self.y = pyb.ADC(self.YPIN)    # create an analog object from a pin

   def readX(self):
      return self.x.read()

   def readY(self):
      return self.y.read()

   def readSwitch(self):
      return not self.BUTTONPIN.value() # If this returns true, the switch is pressed down. Otherwise, the switch is not pressed.


class LCD: 
   # Define some device constants
   LCD_WIDTH = 16    # Maximum characters per line
   LCD_CHR = True
   LCD_CMD = False

   LCD_LINE_1 = 0x80 # LCD RAM address for the 1st line
   LCD_LINE_2 = 0xC0 # LCD RAM address for the 2nd line

   # Timing Constants
   E_PULSE = 0.0005
   E_DELAY = 0.0005

   def __init__(self):
      # LCD Pin Connections
      self.LCD_E = Pin(Pin.cpu.B9, mode=Pin.OUT)
      self.LCD_RS = Pin(Pin.cpu.C9, mode=Pin.OUT)
      self.RWPIN = Pin(Pin.cpu.B8, mode=Pin.OUT)
      self.LCD_D4 = Pin(Pin.cpu.C8, mode=Pin.OUT)
      self.LCD_D5 = Pin(Pin.cpu.A10, mode=Pin.OUT)
      self.LCD_D6 = Pin(Pin.cpu.B3, mode=Pin.OUT)
      self.LCD_D7 = Pin(Pin.cpu.B5, mode=Pin.OUT)
       
      self.RWPIN.low()
      self.lcd_byte(0x01,self.LCD_CMD) # 000001 Clear display -- This line may be unnessesary
      self.lcd_byte(0x33,self.LCD_CMD) # 110011 Initialise
      self.lcd_byte(0x32,self.LCD_CMD) # 110010 Initialise
      self.lcd_byte(0x06,self.LCD_CMD) # 000110 Cursor move direction
      self.lcd_byte(0x0C,self.LCD_CMD) # 001100 Display On,Cursor Off, Blink Off
      self.lcd_byte(0x28,self.LCD_CMD) # 101000 Data length, number of lines, font size
      self.lcd_byte(0x01,self.LCD_CMD) # 000001 Clear display
      time.sleep(self.E_DELAY)

   def lcd_byte(self, bits, mode):
      # Send byte to data pins
      # bits = data
      # mode = True  for character
      #        False for command
      if mode:
         self.LCD_RS.high() # RS
      else:
         self.LCD_RS.low() # RS
      upper = ((bits>>4)&0x0f);

      # High bits
      self.LCD_D4.low()
      self.LCD_D5.low()
      self.LCD_D6.low()
      self.LCD_D7.low()
      if upper&0b00000001==0b00000001:
         self.LCD_D4.high()
      if upper&0b00000010==0b00000010:
         self.LCD_D5.high()
      if upper&0b00000100==0b00000100:
         self.LCD_D6.high()
      if upper&0b00001000==0b00001000:
         self.LCD_D7.high()
        
      # Toggle 'Enable' pin
      self.lcd_toggle_enable()
      lower = ((bits)&0x0f);

      # Low bits
      self.LCD_D4.low()
      self.LCD_D5.low()
      self.LCD_D6.low()
      self.LCD_D7.low()
      if lower&0b00000001==0b00000001:
         self.LCD_D4.high()
      if lower&0b00000010==0b00000010:
         self.LCD_D5.high()
      if lower&0b00000100==0b00000100:
         self.LCD_D6.high()
      if lower&0b00001000==0b00001000:
         self.LCD_D7.high()
        
      # Toggle 'Enable' pin
      self.lcd_toggle_enable()

   def lcd_toggle_enable(self):
      # Toggle enable
      time.sleep(self.E_DELAY)
      self.LCD_E.high()
      time.sleep(self.E_PULSE)
      self.LCD_E.low()
      time.sleep(self.E_DELAY)

   def lcd_string(self, message,line):
      # Send string to display
      MESSAGE_SPACE = self.LCD_WIDTH-len(message)
      i=0
      while i<MESSAGE_SPACE:
         message = message + " "
         i+=1 
      self.lcd_byte(line, self.LCD_CMD)
      for i in range(self.LCD_WIDTH):
         self.lcd_byte(ord(message[i]),self.LCD_CHR)
         
   def lcd_cursor(self, row, col):
        if row == 0:
            col |= 0x80
        elif row == 1:
            col |= 0xC0
        self.lcd_byte(col, False)


class StepperMotor: 

   NEMA_FULL_ROTATION = 1600
   OTHER_FULL_ROTATION = 385

   PMUL_PDIV_ADDR =        0b00010010
   TYPE_VER_ADDR =         0b01110011
   ENABLE_ADDR =           0b01101000 
   VMIN_ADDR =             0b00000100
   VMAX_ADDR =             0b00000110
   PULSE_RAMP_ADDR =       0b00011000 
   AMAX_ADDR =             0b00001100
   MODE_ADDR =             0b01110010
   XACTUAL_ADDR =          0b00000010
   XTARGET_ADDR =          0b00000000
   VTARGET_ADDR =          0b00001000
   LIMIT_SWITCHES_ADDR =   0b00010100
   
   #accelerationValue = 0b00000001

   def __init__(self, chipSelect, acceleration, vMin, vMax, vMode):
      # Polarity = 1, Phase = 1
      # Pin Set-Up
      self.vMode = vMode
      self.accelerationValue = acceleration
      self.vMin = vMin
      self.vMax = vMax
      self.chipSelect = chipSelect
      self.PC6 = Pin("C6", mode = Pin.OUT_PP)
      self.tim = pyb.Timer(3, period = 3, prescaler = 0)
      self.clk = self.tim.channel(1, pin = self.PC6, mode = pyb.Timer.PWM, pulse_width = 2) #Channel 1 or 2?
      self.nCS1 = Pin("C0", mode = Pin.OUT, value = 1)
      self.nCS2 = Pin("B0", mode = Pin.OUT, value = 1)
      self.en1 = Pin("C3", mode = Pin.OUT, value = 0)
      self.en2 = Pin("C2", mode = Pin.OUT, value = 0)
      # SPI Set-Up
      self.spi = SPI(2, SPI.CONTROLLER, baudrate=1000000, polarity=1, phase = 1, firstbit = SPI.MSB) 

      # Calculate the correct pdiv from an acceleration value.
      pmul, pdiv = self.set_accel(self.accelerationValue)
       
      # Populate the byte sets with the appropriate data for each address.
      calculated_Pdiv = bytearray([self.PMUL_PDIV_ADDR,
                                   0b00000000,
                                   pmul,
                                   pdiv & 0b00001111])
       
      testByteSet = bytearray([self.TYPE_VER_ADDR,
                               0b00000000,
                               0b00000000,
                               0b00000000])
       
      enableByteSet = bytearray([self.ENABLE_ADDR,
                                 0b00000000,
                                 0b00000000,
                                 0b00100000]) 
       
      pulseAndRampDivByteSet = bytearray([self.PULSE_RAMP_ADDR,
                                          0b00000000,
                                          0b01110111, # 0b01110111 for microsteps
                                          0b00000000]) 
       
      aMaxByteSet = bytearray([self.AMAX_ADDR,
                               0b00000000,
                               0b00000000,
                               self.accelerationValue]) 
       
      vrampModeByteSet = bytearray([self.MODE_ADDR,
                                    0b00000000,
                                    0b00000000,
                                    0b00000010])
       
      xrampModeByteSet = bytearray([self.MODE_ADDR,
                                    0b00000000,
                                    0b00000000,
                                    0b00000000])
       
      xTargetByteSet = bytearray([self.XTARGET_ADDR,
                                  0b00000000,
                                  0b00000000,
                                  0b10011011])

      zeroTarget = bytearray([self.XTARGET_ADDR,
                              0b00000000,
                              0b00000000,
                              0b00000000]) 
       
      vTargetByteSet = bytearray([self.VTARGET_ADDR, 
                                  0b00000000,
                                  0b00000000,
                                  0b00000000]) 
       
      limitswitches = bytearray([self.LIMIT_SWITCHES_ADDR, 
                                 0b00000000,
                                 0b00000011,
                                 0b00010000])
      
      readModeByteSet = bytearray([0b01110011,
                                    0b00000000,
                                    0b00000000,
                                    0b00000000])
       
      # Send the byte sets:
      #Motor.sendByteSet(testByteSet)
      
      if vMode:
         self.sendByteSet(enableByteSet)
         self.setVelocity(1000,1023)
         self.sendByteSet(pulseAndRampDivByteSet)
         self.sendByteSet(aMaxByteSet)
         self.sendByteSet(calculated_Pdiv)
         self.sendByteSet(vrampModeByteSet)
         self.sendByteSet(vTargetByteSet)
         print(self.sendByteSet(readModeByteSet))
      else:
         self.sendByteSet(enableByteSet)
         self.setVelocity(self.vMin,self.vMax)
         self.sendByteSet(pulseAndRampDivByteSet)
         self.sendByteSet(aMaxByteSet)
         self.sendByteSet(calculated_Pdiv)
         #self.sendByteSet(vrampModeByteSet)
         #self.sendByteSet(vTargetByteSet)
         self.sendByteSet(xrampModeByteSet)
         self.setXActualToZero()

   def convertIntToBytes(self,value):
      firstByte = value & 0xFF
      secondByte = value >> 8 & 0xFF
      thirdByte = value >> 16 & 0xFF
      return (thirdByte,secondByte,firstByte)
    
   def convertBytesToInt(self,value):
      #return int.from_bytes(value,'big')
      r = 0;
      bitmask = 0xff;
      b1 = value[1]
      b2 = value[2]
      b3 = value[3]

      if ((b1 & 0x80) != 0):
          r |= bitmask << 24
          
      r |= b1 << 16
      r |= b2 << 8
      r |= b3
      return r

   def setVelocity(self, vmin, vmax):
      temp1 = self.convertIntToBytes(vmin)
      temp2 = self.convertIntToBytes(vmax)
      vminByteSet = bytearray([self.VMIN_ADDR,temp1[0],temp1[1],temp1[2]])
      vmaxByteSet = bytearray([self.VMAX_ADDR,temp2[0],temp2[1],temp2[2]]) 
      self.sendByteSet(vminByteSet)
      self.sendByteSet(vmaxByteSet)
        
   def sendByteSet(self, byteSet):
         if self.chipSelect == 1:
            self.nCS1.low()
            data = self.spi.send_recv(byteSet)
            #print(data)
            self.nCS1.high()
            return data
         elif self.chipSelect == 2:
            self.nCS2.low()
            data = self.spi.send_recv(byteSet)
            #print(data)
            self.nCS2.high()
            return data
         else:
            return None

    
   def set_accel(self, max_accel):
      pd = range(14)
      pm = range(128,256)
      pmul = 128
      valid = 0
      while pmul<len(pm)+128:
         pdiv = 0
         while pdiv<len(pd):
            q = (pmul/max_accel)*2**(4-pdiv)
            if q>0.095 and q<1:
               valid = 1
               break
            else:
               pdiv += 1
         if valid == 1:
            break
         else:
            pmul += 1
            
      print ("PMUL: ", pmul, "PDIV: ", pdiv)
      return pmul, pdiv

   def sendPosition(self, position):
      targetValue = self.convertIntToBytes(position)
      target = bytearray([self.XTARGET_ADDR,
                           targetValue[0],
                           targetValue[1],
                           targetValue[2]])
      self.sendByteSet(target)
    
   def readPosition(self):
      result = bytearray([0b00000011,
                           0,
                           0,
                           0])
      currentPosition = self.sendByteSet(result)
      answer = self.convertBytesToInt(currentPosition)
      return answer
    
   def travelToPosition(self, position):
       self.sendPosition(position)
       currentPosition = self.readPosition()
       # Return True if motor made it to the target position, False otherwise.
       return currentPosition == position

   def convertIntToBytes(self, value):
      first = value & 0xFF
      second = value >> 8 & 0xFF
      third = value >> 16 & 0xFF
      return (third, second, first)
    
   def setXActualToZero(self):
      vModeByteSet = bytearray([self.MODE_ADDR,
                                    0b00000000,
                                    0b00000000,
                                    0b00000010])
      xrampModeByteSet = bytearray([self.MODE_ADDR,
                                    0b00000000,
                                    0b00000000,
                                    0b00000000])
      xActualByteSet = bytearray([self.XACTUAL_ADDR,
                                  0b00000000,
                                  0b00000000,
                                  0b00000000])
      self.sendByteSet(vModeByteSet)
      self.sendByteSet(xActualByteSet)
      self.sendByteSet(xrampModeByteSet)

def main():
   selected = ""
   filenames = ["Free Draw"]
   for x in os.listdir():
      if x.endswith(".hpgl") and not x.startswith('._'):
         # Prints only text file present in My Folder
         filenames.append(x)
            
   # Initialize objects from each class.
   light = LED()
   pen = Solenoid()
   stick = Joystick()
   display = LCD()
   
   UIMode = True
   freeDrawMode = False
   
   if UIMode:
      i = 0
      line1 = filenames[i]
      line2 = filenames[i+1]
      while UIMode:
         if (stick.readX() > 3048) and i < len(filenames)-1 and i >= 0:
            print("DOWN")
            i+=1
         elif (stick.readX() < 1048) and i <= len(filenames)-1 and i > 0:
            print("UP")
            i-=1
        
         if i == len(filenames)-1 and (i % 2 == 0):
            line1 = filenames[i]
            if (i+1) < len(filenames):
               line2 = filenames[i+1]
            else:
               line2 = ""
         elif i <= len(filenames)-1 and not i == 1:
            if (i+1) < len(filenames):
               line1 = filenames[i]
               line2 = filenames[i+1]
         elif i == 1:
            line1 = filenames[i-1]
            line2 = filenames[i]
            
        
         if (i % 2 == 0):
            display.lcd_string(">" + line1, display.LCD_LINE_1)
            display.lcd_string(line2, display.LCD_LINE_2)
         else:
            display.lcd_string(line1, display.LCD_LINE_1)
            display.lcd_string(">" + line2, display.LCD_LINE_2)
        
         if (stick.readSwitch()):
            light.on()
            UIMode = False
            selected = filenames[i]
            print("Selected:", selected)
            if selected == "Free Draw":
                freeDrawMode = True
            #lcd_byte(0b00000001,LCD_CMD) # 000001 Clear display
            #time.sleep(3)
         else:
            light.off()
            
        #time.sleep(1)
   if not UIMode:
       if freeDrawMode:
           motor_radial = StepperMotor(1, 0b00010000, 1023, 1023, True)

           motor_theta = StepperMotor(2, 0b00000001, 1000, 1023, True)

           #motor_radial.setVelocity(3000,5000)
           #motor_theta.setVelocity(3000,5000)
   
           radius = 0  # This should correspond to where the robot starts
           theta = 0   # This should correspond to where the robot starts
           while True:

            #       THETA_SCALAR = 35 
            #       RADIUS_SCALAR = 35
            # 
            #       radius = radius + int((stick.readY()-2048) / 4096 * THETA_SCALAR)
            #       theta = theta + int((stick.readX()-2048) / 4096 * RADIUS_SCALAR)
            


              theta_speed = -1*(stick.readY()-2048)
              radial_speed = -1*(stick.readX()-2048)
      
              if abs(radial_speed) > 200:
                  targetY = motor_radial.convertIntToBytes(radial_speed)    
              else:
                  radial_speed = 0
                  targetY = motor_radial.convertIntToBytes(0)
      
              if abs(theta_speed) > 200:
                  targetX = motor_theta.convertIntToBytes(theta_speed)   
              else:
                  theta_speed = 0
                  targetX = motor_theta.convertIntToBytes(0)
      

              radialTargetByteSet = bytearray([motor_radial.VTARGET_ADDR, 
                                  targetY[0],
                                  targetY[1],
                                  targetY[2]])
      
              thetaTargetByteSet = bytearray([motor_theta.VTARGET_ADDR, 
                                  targetX[0],
                                  targetX[1],
                                  targetX[2]]) 
      
              line1 = "Theta: " + str(theta_speed)
              line2 = "Radius: " + str(radial_speed)
              display.lcd_string(line1, display.LCD_LINE_1)
              display.lcd_string(line2, display.LCD_LINE_2)
      
              motor_radial.sendByteSet(radialTargetByteSet)
              motor_theta.sendByteSet(thetaTargetByteSet)
              print("Here")
              #print(motor_radial.readPosition())
        #       print(motor_radial.travelToPosition(radius))
        #       print(motor_theta.travelToPosition(theta))

              # If the joystick button is pressed, turn the light on and toggle the pen up/down.
              if (stick.readSwitch()):
                 light.on()
                 # Toggle Pen Up/Down
                 if pen.getValue():
                    pen.down()
                 else:
                    pen.up()
              else:
                 light.off()
       
       if not freeDrawMode:
           motor_radial = StepperMotor(1, 0b00010000, 1023, 1023, False)
           motor_radial.setXActualToZero()
           motor_theta = StepperMotor(2, 0b00000001, 1000, 1023, False)
           motor_theta.setXActualToZero()
            #    radial_speed = 2000
            #       
            # 
            #    targetY = motor_radial.convertIntToBytes(radial_speed)    
            #       
            # 
            #    radialTargetByteSet = bytearray([motor_radial.VTARGET_ADDR, 
            #                                   targetY[0],
            #                                   targetY[1],
            #                                   targetY[2]])
      
      
            #motor_radial.sendByteSet(radialTargetByteSet)
   
            #    motor_radial.setVelocity(3000,5000)
            #    motor_theta.setVelocity(3000,5000)
   
           radius = 0  # This should correspond to where the robot starts
           theta = 0   # This should correspond to where the robot starts
   
           # Parse the input:
           # Get filename from the command-line arguments.
           
           args = []
           commands = []
           filename = selected
   
        #    if (motor_radial.travelToPosition(0)) and (motor_theta.travelToPosition(0)):
        #        pass

           if filename:
              with open(filename) as f:
                 # Store all the lines of the file into the lines array.
                 lines = f.readlines()
              # Split this string into an array of elements.
    
           for i in range(0, len(lines)):
              formattedLine = lines[i]
              #print(formattedLine)
              # Remove extraneous newline characters.
              if '\n' in formattedLine: 
                 formattedLine = formattedLine.replace('\n', '')
                 # Remove extraneous spaces.
              if ' ' in formattedLine: 
                 formattedLine = formattedLine.replace(' ', '')

              # Split each line by its semicolons to identify the commands.
              splitBySemicolon = formattedLine.split(';')
              # print(splitBySemicolon)
              for i in range(0, len(splitBySemicolon)):
                 commands.append(splitBySemicolon[i][:2])
                 args.append(splitBySemicolon[i][2:].split(','))
              #print("Commands", commands)
              #print("Args", args)

           datax = []
           datay = []
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

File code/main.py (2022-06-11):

"""!
@file main.py
@author Ryan Dean, Mike Eirenberg, Ben Bradley
@date 6/9/2022

This is the main file to run the pen plotter, containing all tasks
used for cooperative multitasking. In this you will find four tasks;
File Draw, and Free_Draw,  Calc_HPGL, UI. Refer to the Readme.md for
more information on each task. 

"""

import gc
import cotask
import task_share
from ulab import numpy as np
import math
import pyb
from pyb import Pin, Timer, ADC, ExtInt, SPI
import time
import array
import os
import stepperMotor
import lcd
import solenoid
import led
import joystick
global args, commands

def File_Draw():
    
    """
    This task is responsible for taking processed HPGL data and
    sending it to the stepper motors. The radial motor is set with
    a much higher acceleration than the theta motor because
    the theta motor has much more interia to move and therefore
    will need more time to accelerate and decelerate the pen
    plotter assembly.
    """
    
    # Initializes motors in Ramp Mode
    motor_radial = stepperMotor.StepperMotor(1, 0b00001000, 1000, 1500, False)
    motor_theta = stepperMotor.StepperMotor(2, 0b00000001, 1000, 1023, False)
    
    # Sets starting position as homing prosition when done printing
    motor_radial.setXActualToZero()
    motor_theta.setXActualToZero()
    
    # Turns LED light on
    light.on()
    
    # LCD display commands
    line1 = "Print Started"
    line2 = ""
    display.lcd_string(line1, display.LCD_LINE_1)
    display.lcd_string(line2, display.LCD_LINE_2)
    
    while True:
        if state.get() == 3:                
            # This ensures the motor reaches the first drawing point before the
            # plotting pen goes down
            if mode.get() == 0:
                # Returned value is True when position is reached, False otherwise
                bool1 = motor_theta.travelToPosition(int(datax[ii.get()]),10)
                bool2 = motor_radial.travelToPosition(int(datay[ii.get()]),10)
                if (bool1 and bool2):
                    pen.down() # Controls plotting pen
                    mode.put(1)
                    ii.put(1) # Used for data indexing
            
            elif mode.get() == 1:
                # Iterates through Theta (datax) and Radial (datay),
                # sending positions to motors
                bool1 = motor_theta.travelToPosition(int(datax[ii.get()]),0)
                bool2 = motor_radial.travelToPosition(int(datay[ii.get()]),0)
                
                
                if not CancelButton.value():
                    # Print cancellation when blue button on STM 32 pressed
                    print('Free Draw Cancelled')
                    print('Cancellation Activated')
                    state.put(0)
                    light.on()
                    pen.up()
                    
                    # LCD commands
                    line1 = "Print Cancelled"
                    line2 = ""
                    display.lcd_string(line1, display.LCD_LINE_1)
                    display.lcd_string(line2, display.LCD_LINE_2)
                    
                    # Tells motors to return to homing position
                    motor_theta.travelToPosition(0,0)
                    motor_radial.travelToPosition(0,0)
                    mode.put(0)
                
                
                if (bool1 and bool2):
                    # LCD commands to update LCD each time the motor reaches
                    # its desired position
                    p = ii.get()
                    print("Got to point")
                    
                    # LCD commands
                    line1 = "Printing..."
                    line2 = "Point " + str(p) + " of " + str(len(datax))
                    display.lcd_string(line1, display.LCD_LINE_1)
                    display.lcd_string(line2, display.LCD_LINE_2)
                    ii.put(ii.get()+1)
                    
                    # Checks if end of received data has been reached
                    if ii.get() == len(datax):
                        ii.put(0)
                        state.put(0)
                        
                        # Brings pen back up
                        pen.up()
                        
                        # LCD commands                        
                        light.on()
                        line1 = "Print Completed"
                        line2 = ""
                        display.lcd_string(line1, display.LCD_LINE_1)
                        display.lcd_string(line2, display.LCD_LINE_2)
#                         UIMode = True

                        # Tells motors to return to homing position
                        motor_theta.travelToPosition(0,0)
                        motor_radial.travelToPosition(0,0)
                        light.off() # Turns off LED
                        mode.put(0)
                    else:
                        yield None
                else:
                    yield None
        else:
            yield None
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

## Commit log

2022-05-29 Driver Design readme
2022-05-30 lead screw not oriented right in pic
2022-05-30 maybe lead screw will work this time...
2022-05-31 Added file drawing features
    Added drawing cancellation, that sets pen back to its original position when interrupted. User can then select a new drawing
2022-05-31 Some Fixes
    just ask me about this
    [latest.py]
2022-06-01 Has other tasks but with issues
    For whatever reason, both motors will start accelerating and never stop even when bool1 and bool2 are False and it should only be going to its target position. DO NOT HAVE ANY MOTORS TIED DOWN WITH SET SCREWS WHEN RUNNING THIS
2022-06-02 Different Free-Draw Joystick Method
    Radial motor not moving though.
2022-06-02 Stepper Class Updated with Vel and Pos Mode Change
2022-06-05 Compressed Parts and Assemblies
2022-06-05 Individual Components
    [5909K31_Needle-Roller Thrust Bearing.SLDPRT, 90480A007_Low-Strength Steel Hex Nut.SLDPRT, 91251A148_Black-Oxide Alloy Steel Socket Head Screw.SLDPRT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]
2022-06-06 Deleted my kinematics homework, will update soon.
2022-06-07 Kinematics Images
2022-06-07 Updated the kinematics section.
2022-06-07 kinematics images resized
2022-06-07 resized kinematics images
2022-06-07 resized second kinematics image
2022-06-08 3D-Printed Joystick and LCD Housing Model
    Files to redesign or print the joystick and LCD cover.
    [LCDJoystickDisplay.dwg, LCDJoystickDisplay.stl]
2022-06-09 Added Latex Formulas for the Kinematics Section
2022-06-09 testing tabs in the kinematics text
2022-06-09 latex spacing changes for kinematics section
2022-06-09 Added Wiring Diagram
2022-06-10 Kinematics Image for Website Description
2022-06-10 Added Kinematics Image
